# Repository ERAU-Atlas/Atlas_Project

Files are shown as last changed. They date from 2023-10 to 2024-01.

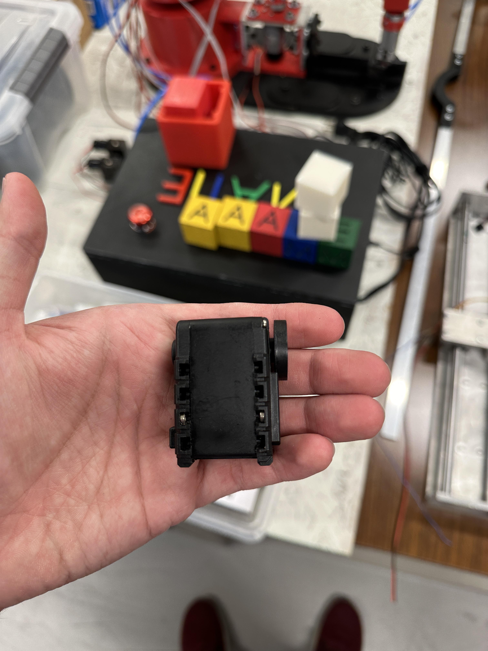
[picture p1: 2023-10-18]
Prelim/Milestones/Coceptual Design/Group CoDR/Group Conceptual Design Images/Servo pics/IMG_5382.jpeg

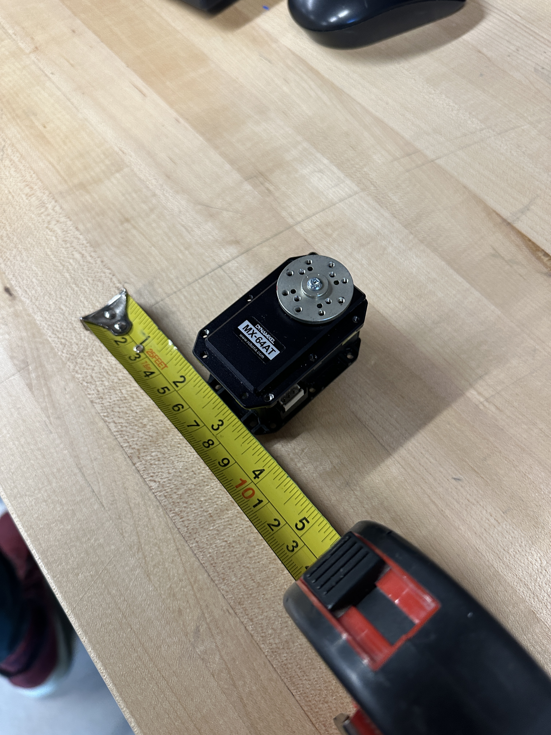
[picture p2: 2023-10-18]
Prelim/Milestones/Coceptual Design/Group CoDR/Group Conceptual Design Images/Servo pics/IMG_5388.jpeg

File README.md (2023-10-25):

# Atlas Project
The Atlas project is an ongoing robotics capstone design project at Embry-Riddle Aeronautical University. 
Our goal is to design and create a better way for furniture movement within residential buildings, to decrease the damages that accompany such moves.

## Documentation and other information can be found in the project [Wiki](https://github.com/ERAU-Atlas/Atlas_Project/wiki)

***

## Future Development notes and information will be noted below

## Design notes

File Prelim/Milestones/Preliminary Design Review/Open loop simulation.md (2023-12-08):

$$
F = \sum\limits_{i=1}^{N} F_{i}
$$

software flowchart instead of gantt chart

callouts instead of bullets

 resize top right pictures

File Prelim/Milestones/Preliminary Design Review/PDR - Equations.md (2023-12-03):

vector originating at B and terminating at C measured with respect to frame A

direction cosine matrix with columns that are the unit-basis vectors of frame B measured with respect to frame A

angular velocity of coordinate frame B relative to frame C measured with respect to frame A

matrix of moments of inertia and products of inertia of body B measured with respect to frame A

vector of first mass moments of body B measured in with respect to frame A

mass of body/particle i

translational momentum of body/particle i measured with respect to frame A

angular momentum of body/particle i about the origin of frame B measured with respect to frame A

force applied to body/particle i measured with respect to frame A

moment on body/particle i about point B measured with respect to frame A

vector of system forces along the system coordinates ${\boldsymbol a}$

***
Equations of motion:
$$
\boldsymbol{H}(\boldsymbol{\gamma})\ddot{\boldsymbol{\gamma}} + \boldsymbol{d}(\boldsymbol{\gamma}, \dot{\boldsymbol{\gamma}}) = \boldsymbol{F}_{\boldsymbol{\gamma}}
$$

***
position and orientation of Atlas:

$$
{^{I}_{I}{\boldsymbol{r}}_{F}} = \begin{bmatrix}\delta x \\ \delta y \\ \delta z\end{bmatrix}
$$
$$
{^{I}\boldsymbol{T}}_{\!F} = \left[\begin{array}{ccc} \cos\left(\psi \right)\,\cos\left(\theta \right) & -\cos\left(\theta \right)\,\sin\left(\psi \right) & \sin\left(\theta \right)\\ \cos\left(\phi \right)\,\sin\left(\psi \right)+\cos\left(\psi \right)\,\sin\left(\phi \right)\,\sin\left(\theta \right) & \cos\left(\phi \right)\,\cos\left(\psi \right)-\sin\left(\phi \right)\,\sin\left(\psi \right)\,\sin\left(\theta \right) & -\cos\left(\theta \right)\,\sin\left(\phi \right)\\ \sin\left(\phi \right)\,\sin\left(\psi \right)-\cos\left(\phi \right)\,\cos\left(\psi \right)\,\sin\left(\theta \right) & \cos\left(\psi \right)\,\sin\left(\phi \right)+\cos\left(\phi \right)\,\sin\left(\psi \right)\,\sin\left(\theta \right) & \cos\left(\phi \right)\,\cos\left(\theta \right) \end{array}\right]
$$
Where:
$\delta x$ = displacement in the x direction
$\delta y$ = displacement in the y direction
$\delta z$ = displacement in the z direction
$\phi$ = angle about the x axis
$\theta$ = angle about the y axis
$\psi$ = angle about the z axis

***

$$
\boldsymbol{{^{I}_{I}{\boldsymbol{r}}_{F}}} = \begin{bmatrix}\delta x \\ \delta y \\ \delta z\end{bmatrix}
$$

$$
{^{I}\boldsymbol{T}}_{\!F} = 
$$

$$
\left[\begin{array}{ccc} \cos\left(\psi \right)\,\cos\left(\theta \right) & -\cos\left(\theta \right)\,\sin\left(\psi \right) & \sin\left(\theta \right)\\ \cos\left(\phi \right)\,\sin\left(\psi \right)+\cos\left(\psi \right)\,\sin\left(\phi \right)\,\sin\left(\theta \right) & \cos\left(\phi \right)\,\cos\left(\psi \right)-\sin\left(\phi \right)\,\sin\left(\psi \right)\,\sin\left(\theta \right) & -\cos\left(\theta \right)\,\sin\left(\phi \right)\\ \sin\left(\phi \right)\,\sin\left(\psi \right)-\cos\left(\phi \right)\,\cos\left(\psi \right)\,\sin\left(\theta \right) & \cos\left(\psi \right)\,\sin\left(\phi \right)+\cos\left(\phi \right)\,\sin\left(\psi \right)\,\sin\left(\theta \right) & \cos\left(\phi \right)\,\cos\left(\theta \right) \end{array}\right]
$$

***

$$
{^{I}_{I}{\boldsymbol{r}}_{A3}} = {^{I}_{I}{\boldsymbol{r}}_{F}} + {^{I}\boldsymbol{T}}_{\!F} {^{F}_{F}{\boldsymbol{r}}_{A1}} + {^{I}\boldsymbol{T}}_{\!F} {^{F}\boldsymbol{T}}_{\!A1} {^{A1}_{A1}{\boldsymbol{r}}_{A2}} + {^{I}\boldsymbol{T}}_{\!F} {^{F}\boldsymbol{T}}_{\!A1} {^{A1}\boldsymbol{T}}_{\!A2} {^{A2}_{A2}{\boldsymbol{r}}_{A3}}
$$
$$
{^{I}\boldsymbol{T}}_{\!A3} = {^{I}\boldsymbol{T}}_{\!F} {^{F}\boldsymbol{T}}_{\!A1} {^{A1}\boldsymbol{T}}_{\!A2} {^{A2}\boldsymbol{T}}_{\!A3}
$$

where:
${^{I}_{I}{\boldsymbol{r}}_{1}}$
${_I^I}\mathbit{r}_1$

${^{A}_{B}{\boldsymbol{r}}_{}}$
${_B^A}r$

Planar two link IK:
$$
\theta_{2}= atan2\left(\pm \sqrt{1 - \left( \frac{z_{d}^{2} + y_{d}^{2} - l_{1}^{2} - l_{2}^{2}}{2l_{1}^{2}l_{2}^{2}}\right)^{2}}, \frac{z_{d}^{2} + y_{d}^{2} - l_{1}^{2} - l_{2}^{2}}{2l_{1}^{2}l_{2}^{2}} \right)
$$

$$
\begin{align*}
K_{1} &= l_{1} + l_{2} \cos(\theta_{2})\\
K_{2} &= l_{2}\sin(\theta_{2})
\end{align*}
$$

$$
\theta_{1} = atan2\left( z_{d}, y_{d} \right) - atan2\left( K_{2}, K_{1} \right)
$$

$$
{^{I}_{I}{\boldsymbol{r}}_{A3}} = {^{I}_{I}{\boldsymbol{r}}_{F}} + {^{F}_{F}{\boldsymbol{r}}_{A1}} + {^{A1}_{A1}{\boldsymbol{r}}_{A2}} + {^{A2}_{A2}{\boldsymbol{r}}_{A3}}
$$

$$
{^{I}_{I}{\boldsymbol{r}}_{A3}} = {^{I}_{I}{\boldsymbol{r}}_{F}} + {^{I}\boldsymbol{T}}_{\!F} {^{F}_{F}{\boldsymbol{r}}_{A1}} + {^{I}\boldsymbol{T}}_{\!F} {^{F}\boldsymbol{T}}_{\!A1} {^{A1}_{A1}{\boldsymbol{r}}_{A2}} + {^{I}\boldsymbol{T}}_{\!F} {^{F}\boldsymbol{T}}_{\!A1} {^{A1}\boldsymbol{T}}_{\!A2} {^{A2}_{A2}{\boldsymbol{r}}_{A3}}
$$

$$
{^{I}_{I}{\boldsymbol{r}}_{A3}} = {^{I}_{I}{\boldsymbol{r}}_{F}} + {^{I}\boldsymbol{T}}_{\!F} {^{F}_{F}{\boldsymbol{r}}_{A1}} + {^{I}\boldsymbol{T}}_{\!A1} {^{A1}_{A1}{\boldsymbol{r}}_{A2}} + {^{I}\boldsymbol{T}}_{\!A2} {^{A2}_{A2}{\boldsymbol{r}}_{A3}}
$$

***
Equations of motion

$$
\boldsymbol{H}(\gamma)\ddot{\gamma} + \boldsymbol{d}(\gamma, \dot{\gamma}) = \boldsymbol{F}_{\gamma}
$$

$$
\ddot{\boldsymbol{\gamma}} = \frac{\boldsymbol{F}_\gamma - \boldsymbol{d}(\gamma, \dot{\gamma})}{\boldsymbol{H}(\gamma)}
$$

$$
\ddot{\boldsymbol{\gamma}} = \frac{F_\gamma -\boldsymbol{d}(\gamma, \dot{\gamma}) + G - B\dot{\gamma} - Csign(\dot{\gamma})}{\boldsymbol{H}(\gamma)}
$$

***
### Runge-Kutta

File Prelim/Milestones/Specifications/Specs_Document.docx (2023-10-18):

SPECIFICATIONS DOCUMENT

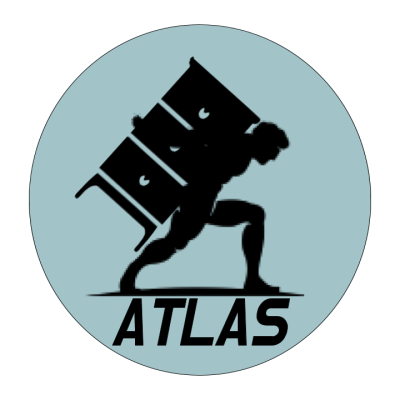
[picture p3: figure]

By

Ian Adelman

Devin Hoopes

Natalie Gonzalez

Alex Reinert

Submitted to Dr. Isenberg and Dr. Adams
of Embry-Riddle Aeronautical University
in Partial Fulfillment of the Course Requirements for ME 407 and COM 420

October 21, 2023

# ABSTRACT

In this document the proposed stair climbing system and its components will be described in detail, and an explanation for each component’s inclusion will be provided. Such explanation will be supplemented with the list of design requirements derived from the problem statement, and how each component/design feature directly contributes to fulfilling the requirements and solving the problem presented.

# 1.0 INTRODUCTION

In this section, the requirements will be laid out in the following categories: Functional, Sizing, and Safety.

## 1.1 PROBLEM STATEMENT

Transporting heavy furniture up and down the stairs is difficult and potentially dangerous.

To achieve the goal set by the problem statement, the requirements of function are as follows:

2.1.1 - The system shall transport furniture repeatedly up and down one floor within a residential building.

and Safety.

## 1.2 SYSTEM OVERVIEW

In this section the system will be shown, and the operation will be described in detail.

### 1.2.1 Components

### 1.2.2 Concept of Operations

The standard practice for operating the device is as follows: First, the user will load the payload furniture onto the platform and then apply securing straps through the side brackets. Next, use the remote control to command the device to begin walking up the set of stairs. Once the device reaches the top of the stairs, undo the straps and remove the furniture from the platform.

### 3.2.1 Process Flowchart

The following flowchart describes the process that the system will follow in order to achieve the problem statement.

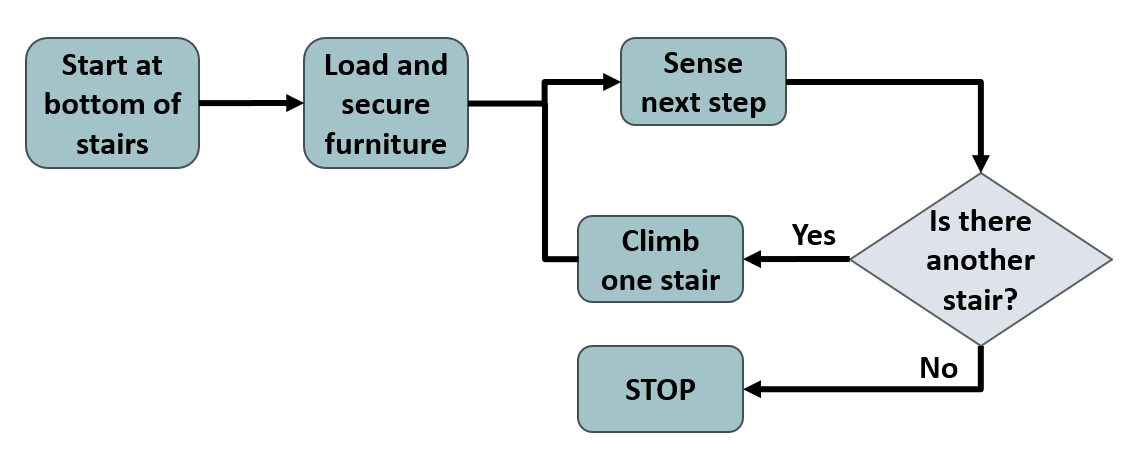
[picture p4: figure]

Figure 3.6: Process Flowchart

### 3.2.2 Hardware Block Diagram

The following block diagram describes the connections and relationships between the various components.

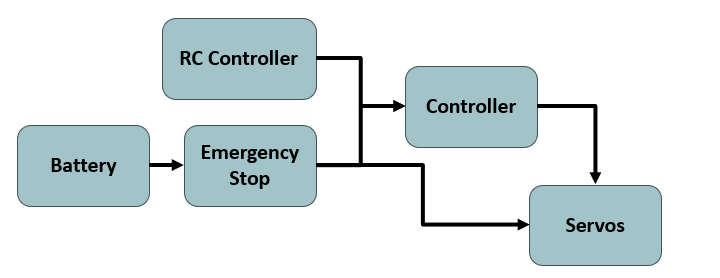
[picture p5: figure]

Figure 3.7: Hardware Block Diagram

# 2.0 REQUIREMENTS

In this section, the requirements will be laid out in the following categories: Functional, Sizing, and Safety.

## 2.1 FUNCTIONAL

To achieve the goal set by the problem statement, the requirements of function are as follows:

2.1.1 - The system shall transport furniture repeatedly up and down one floor within a residential building.

2.1.2 - The system shall accommodate up to a 4-seater sofa.

2.1.3 - The system shall accommodate up to a 5-shelf bookshelf.

2.1.4 - The system shall be reusable.

## 2.2 SIZING

To ensure that the system is of a proper size that is capable of being transported and capable of fitting within the stairwells it operates in, the requirements of interface are as follows:

2.2.1 - The system shall fit within a standard stairway according to Section R311.7.1 of the 2021 International Residential Code (IRC).

2.2.2 - The system shall be transportable in the back of an average American pickup truck in addition to the transported furniture.

## 2.3 SAFETY

To ensure that the system is overall safe, and does not endanger the operator or environment, the requirements of safety are as follows:

2.3.1 - The system shall cause less injury and strain than an average moving job.

2.3.2 - The system shall not destructively alter the environment.

2.3.3 - The system shall not damage the furniture.

# 3.0 SYSTEM OVERVIEW

In this section the system will be shown, and the operation will be described in detail.

## 3.1 SYSTEM COMPONENTS

In this section the system’s components will be described in detail, with an explanation of how each requirement is met through the design’s features.

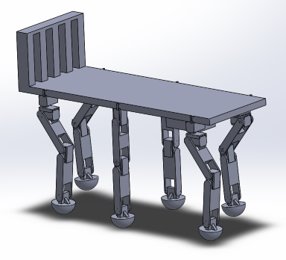
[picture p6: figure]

Electronics

Platform

2 DOF Legs

Brackets

3 DOF Legs

Figure 3.1: Complete Drawing

### 3.1.1 Platform

In the figure below, the dimensions of the platform are shown.

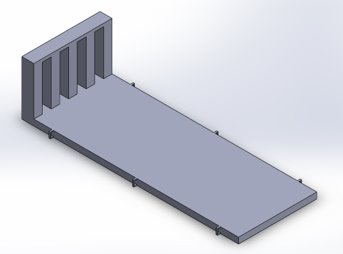
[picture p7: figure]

8”

13”

36”

Figure 3.2: Platform Drawing

To accommodate its payload [2.1.2, 2.1.3] as well as fit into a standard residential stairwell [2.2.1] or pickup truck bed [2.2.2], the system is sized to be 25” at full scale, allowing for an inch of space between the system and the stairs’ thinnest point, the rails.

### 3.1.2 Brackets

In the figure below, the dimensions of the bracket are shown.

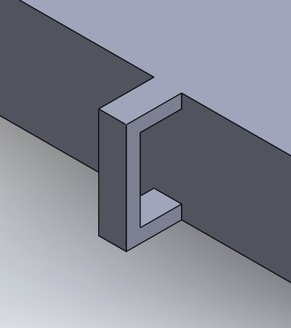
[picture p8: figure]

0.125”

0.25”

1”

Figure 3.3: Bracket Drawing

To prevent the payload from slipping, thus damaging the furniture as well as the surrounding environment [2.3.2, 2.3.3], brackets are located along the edge of the platform to allow for straps to be applied to the payload.

### 3.1.3 Legs

In the figure below, the dimensions of the robotic leg are shown.

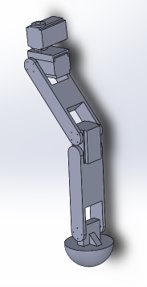
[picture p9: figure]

7.2””

7.2””

Figure 3.4: Robotic Leg Drawing

In order to ascend the stairs [2.1.1] without modifying the surrounding environment [2.3.2], the system will utilize a set of legs for locomotion. The front and back pairs of legs each have 3 degrees of freedom, with a 2 degree of freedom shoulder as well as a 1 degree of freedom elbow provide the majority of the force required to ascend the stairs. Providing stability [2.3.2, 2.3.3] rather than climbing force, the pair of central legs have 2 degrees of freedom each, with a 1 degree of freedom shoulder and elbow. Additionally, to prevent damage to the stairwell flooring [2.3.2] each leg has a semicircular rubber foot.

### 3.1.4 Electronics

In the figure below, the dimensions of the electronics bay are shown.

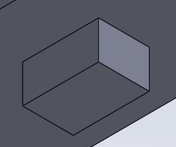
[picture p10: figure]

3”

4”

6”

Figure 3.5: Electronics Bay Drawing

In order for the system to be reusable [2.1.4], the system will have a rechargeable battery. In order to reduce the strain and injury to a person [2.3.1], the system will be remotely controlled. In order to ascend the stairs [2.1.1], the system will have an encoder to detect the depth of each step and the height of the next step.

## 3.2 CONCEPT OF OPERATIONS

The standard practice for operating the device is as follows: First, the user will load the payload furniture onto the platform and then apply securing straps through the side brackets. Next, use the remote control to command the device to begin walking up the set of stairs. Once the device reaches the top of the stairs, undo the straps and remove the furniture from the platform.

### 3.2.1 Process Flowchart

The following flowchart describes the process that the system will follow in order to achieve the problem statement.

Figure 3.6: Process Flowchart

### 3.2.2 Hardware Block Diagram

The following block diagram describes the connections and relationships between the various components.

Figure 3.7: Hardware Block Diagram

# 4.0 CONCLUSION

Through the above features, the system can reliably and safely transport its intended loads up and down a flight of stairs without endangering the operator and while reducing the overall strain on the operator compared to manually moving the payload up the stairs.

# 5.0 APPENDIX

Below is the appendix, including the requirements verification matrix and the decision matrix created for the project.

## 5.1 APPENDIX A – REQUIREMENTS VERIFICATION MATRIX

No. | Requirement | Verification Description | T | A | O | R
1 | 2.1.1 | Test load and trial | X
2 | 2.1.2 | Measurement/Trial | X
3 | 2.1.3 | Measurement/Trial | X
4 | 2.1.4 | Repeated Trials | X | | X
5 | 2.2.1 | Measurement and Comparison | X | | | X
6 | 2.2.2 | Measurement and Comparison | X | | | X
7 | 2.3.1 | Trial, followed by Analysis and Comparison | X | X | X | X
8 | 2.3.2 | Trial and Observation | X | | X
9 | 2.3.3 | Trial and Observation | X | | X

T – Test and Measurement; A – Analysis and Simulation;
O – Observation and Inspection; R – Reference and Datasheet

(Requirements verification matrix. | download table - researchgate) [1]

## 5.2 APPENDIX B – DECISION MATRIX

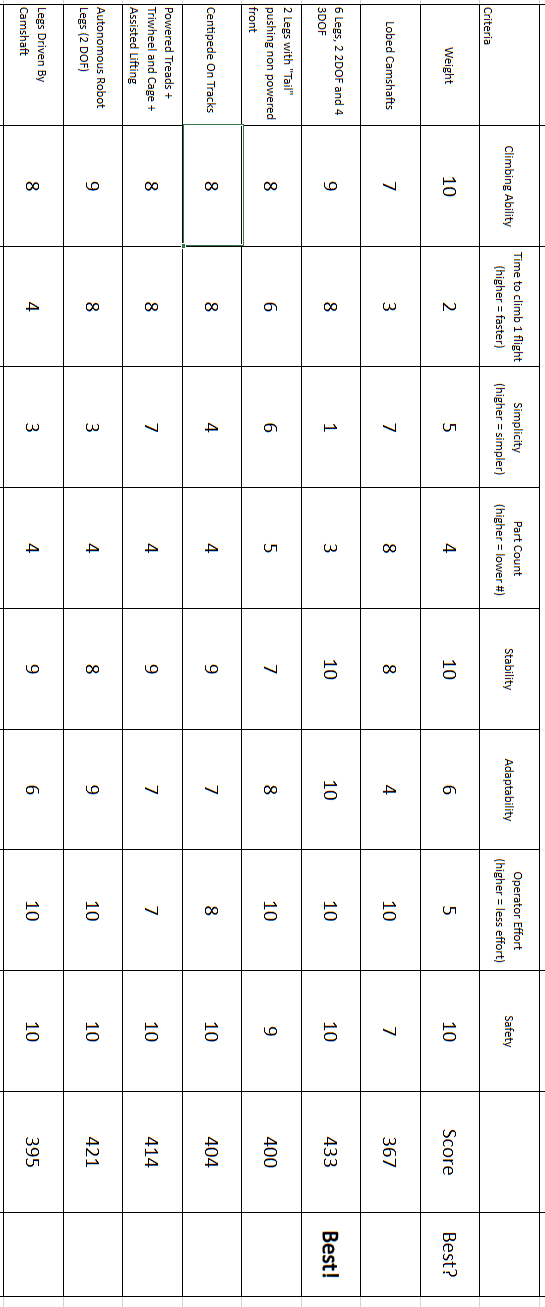
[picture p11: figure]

## 5.3 APPENDIX C – MORPHOLOGICAL CHART

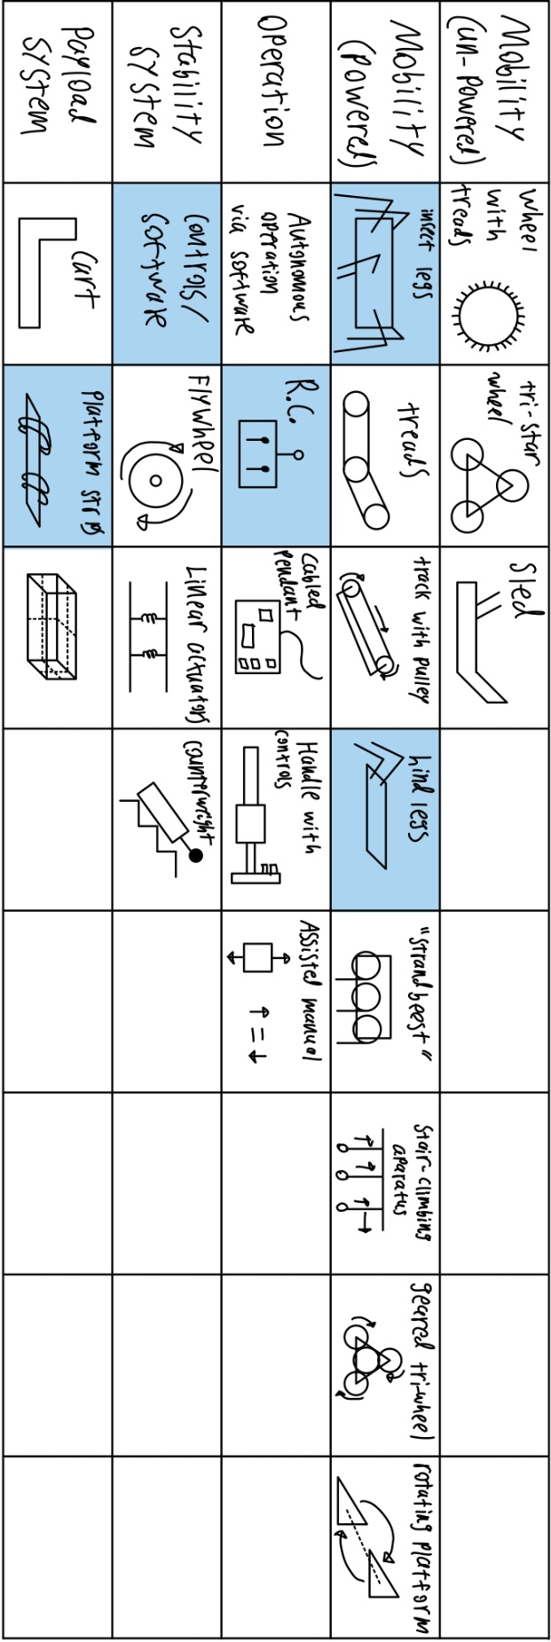
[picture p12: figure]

# 6.0 REFERENCES

[1]
“Requirements verification matrix. | download table - researchgate,” ResearchGate, https://www.researchgate.net/figure/Requirements-Verification-Matrix_tbl1_269163835 (accessed Sep. 28, 2023).

Specs for codes:

https://codes.iccsafe.org/content/IRC2021P2/chapter-3-building-planning

R311.7.1 Width.

Stairways shall be not less than 36 inches (914 mm) in clear width at all points above the permitted’

The maximum width of the system shall not exceed 27 inches at full scale, reducing to a maximum width of 13 inches at the designed scale.

Pull from page, use scale?

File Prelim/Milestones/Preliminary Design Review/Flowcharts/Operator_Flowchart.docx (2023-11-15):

Operator

END

START

Remove straps and PAYLOAD.

Turn OFF system with communications device.

Roll away from stairway.

NO

YES

YES

Done Climbing?

E

Select BOTTOM-STEP CLIMBING mode.

YES

YES

NO

At Bottom Step?

UP or DOWN?

E

E

E

Select DESCENDING mode.

Select FLAT mode.

NO

Done Climbing?

At Landing?

E

NO

NO

At stairway yet?

YES

Select TOP-STEP CLIMBING mode.

Select ASCENDING mode.

UP

E

At Landing?

Select FLAT mode.

Turn ON system with communications device.

Place PAYLOAD on platform and secure with straps.

END

EMERGENCY SHUTOFF

END

Press EMERGENCY BUTTON.

Anything dangerous with operation?

E

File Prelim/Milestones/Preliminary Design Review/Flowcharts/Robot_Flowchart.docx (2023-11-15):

Robot

E

Turn OFF.

Roll away from stairway.

NO

YES

YES

YES

Switch to FLAT mode.

NO

Done Climbing?

NO

At Bottom Step?

Switch to BOTTOM-STEP CLIMBING mode.

Done Climbing?

YES

NO

Switch to TOP-STEP CLIMBING mode.

UP or DOWN?

At Landing?

DOWN

Switch to DESCENDING mode.

UP

Switch to ASCENDING mode.

Drive to stairway.

Switch to FLAT mode.

Turn ON.

START

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
EMERGENCY SHUTOFF

END

SHUT OFF ALL POWER.

YES

NO

EMERGENCY Button Pressed?

E

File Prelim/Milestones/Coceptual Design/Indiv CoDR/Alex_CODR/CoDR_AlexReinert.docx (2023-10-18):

CONCEPTUAL DESIGN DOCUMENT


By

Alex Reinert

Submitted to Dr. Isenberg and Dr. Adams
of Embry-Riddle Aeronautical University
in Partial Fulfillment of the Course Requirements for ME 407 and COM 420

9/29/23

# ABSTRACT

The following document introduces the design that is a solution to the problem statement below. The design’s components and features will be discussed and detailed explanation of how they solve the requirements to the problem.

# 1.0 PROBLEM STATEMENT

Transporting heavy furniture up and down the stairs is difficult and potentially dangerous.

# 2.0 REQUIREMENTS

## 2.1 FUNCTION

To achieve the goal set by the problem statement, the requirements of function are as follows:

2.1.1 - The system shall transport furniture repeatedly up and down one floor within a residential building.

2.1.2 - The system shall accommodate up to a 4-seater sofa.

2.1.3 - The system shall accommodate up to a 5-shelf bookshelf.

2.1.4 - The system shall be reusable.

## 2.2 INTERFACING

To ensure that the system is of a proper size that is capable of being transported and capable of fitting within the stairwells it operates in, the requirements of interface are as follows:

2.2.1 - The system shall fit within a standard stairway according to Section R311.7.1 of the 2021 International Residential Code (IRC)

2.2.2 - The system shall be transportable in the back of an average American pickup truck in addition to the transported furniture.

## 2.3 SAFETY

To ensure that the system is overall safe, and does not endanger the operator or environment, the requirements of safety are as follows:

2.3.1 - The system shall cause less injury and strain than an average moving job.

2.3.2 - The system shall not destructively alter the environment.

2.3.3 - The system shall not damage the furniture.

# 3.0 SYSTEM OVERVIEW

## 3.1 CONCEPT OF OPERATIONS

The standard practice for using the proposed device is as follows: First, the user will load the furniture onto the flat platform and put on securing straps to ensure the furniture is stable. Second, the user will place it in front on the stairs. Third, the user will turn on the hardware and motors will begin to run. Fourth, the ultrasonic sensor will detect a stairway and begin increasing speed to the motors. Fifth, the tilt sensor will sense that we are approaching a landing and will slow down the motors. Sixth, the system will stop after reaching the landing. Finally, the straps will be removed, and furniture will be picked up and placed where it is needed.

## 3.2 SYSTEM DESIGN

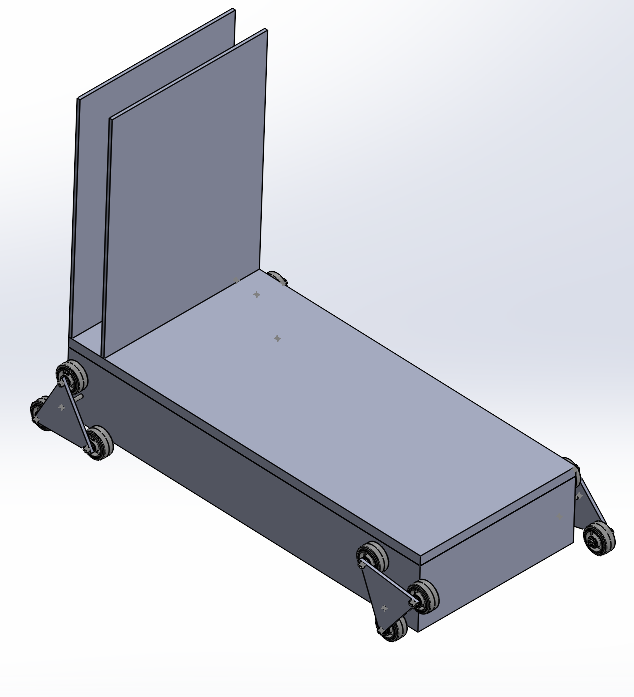
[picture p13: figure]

Tri-Star Wheel

Electronic Storage

Composite Bed

Spring-Backing

### 3.2.1 Composite Bed

The system includes a flat platform where the furniture is set and secured before operation. The furniture rests on the flat platform and is kept secure with straps ensuring both the safety of the furniture itself and the environment around it, satisfying requirements 2.3.2 and 2.3.3. The platform is sized so that its width does not exceed 26.5 inches and 60 inches long. This is big enough to support a 4-seater sofa and a 5-shelf bookshelf, satisfying requirements 2.1.2 and 2.1.3. This will also fit into the back of a pickup truck and meet the standard of the minimum width of a stairwell according to the IRC residential code, this satisfies requirements 2.2.1 and 2.2.2.

### 3.2.2 Tri-Star Wheel

The system is driven by four DC motors attached to four triangles. The motor drives an axle located at the center of each triangle. The system also includes three wheels attached by an axle to each point on the triangle. Both feature’s help meet requirement 2.1.1.

### 3.2.3 Spring-Backing

The system is fitted with four compression springs in between two rectangular plates, which provides support to the system. This Spring-Backing can compress to support heavy weight moving up or down the stairs, satisfying requirement 2.1.4.

### 3.2.4 Electronics

The system is fitted with a rechargeable battery located in the Electronic Storage, which provides the necessary power to the rest of the system satisfying requirement 2.1.4. The system also includes two sensors, an ultrasonic sensor and a tilt sensor, this will ultimately control the motor speed, satisfying requirements 2.3.1 and 2.3.3. The system also includes four DC motors that turn the Tri-Star Wheel, satisfying requirement 3.3.1.

### 3.2.5 Software

The software design is to take input from the ultrasonic sensor to see how far away the staircase is and a tilt sensor to detect when we are on a landing or on the stairs. It then takes this information to compute the appropriate motor speed in order to elevate up the stairs.

## 3.3 OTHER SOLUTIONS

### 3.3.1 Stair Climber for Caskets

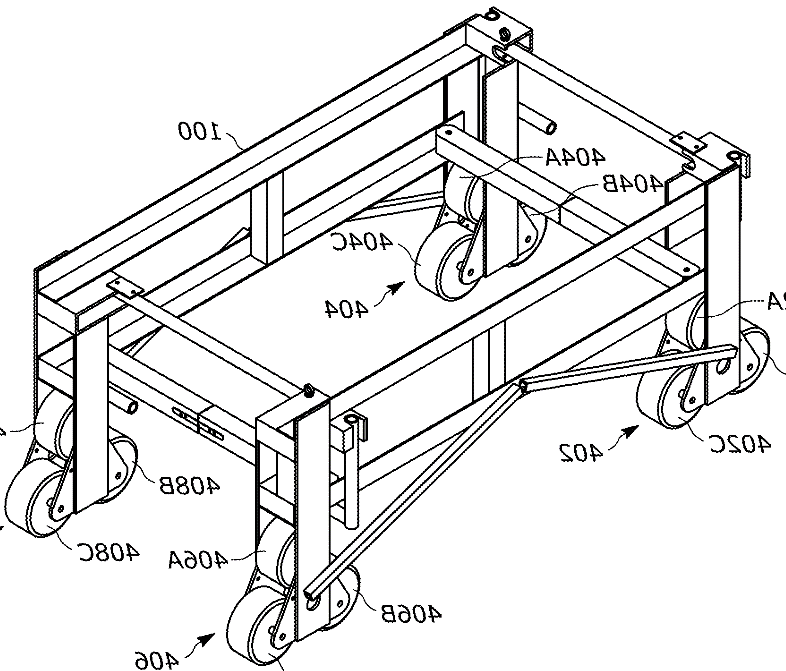
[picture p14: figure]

Tri-Star Wheel

The image above is the Stair Climber for Caskets invented by Samuel Polumbo. This design is not powered and intended for a user to grab the handles and pull the device up the stairs. It moves up the stairs with the Tri-Star Wheel pivoting up each step.

# 4.0 CONCLUSION

From the above features and components, the system can safely and securely move furniture up or down the stairs. It can accommodate the intended furniture that is to be placed on it and not endanger the user of the system.

# 5.0 APPENDIX

No. | Requirement | Verification Description | T | A | O | R
1 | 2.1.1 | Test load and trial | X
2 | 2.1.2 | Measurement/Trial | X
3 | 2.1.3 | Measurement/Trial | X
4 | 2.1.4 | Repeated Trials | X | | X
5 | 2.2.1 | Measurement and Comparison | X | | | X
6 | 2.2.2 | Measurement and Comparison | X | | | X
7 | 2.3.1 | Trial, followed by Analysis and Comparison | X | X | X | X
8 | 2.3.2 | Trial and Observation | X | | X
9 | 2.3.3 | Trial and Observation | X | | X

T – Test and Measurement; A – Analysis and Simulation;
O – Observation and Inspection; R – Reference and Datasheet

(Requirements verification matrix. | download table - researchgate) [1]

# 6.0 ACKNOWLEDGEMENTS

This design directly implemented the Tri-Star Wheel from the casket stair climber, which was invented by Samuel Palumbo, found in US patent US11691660B2 [2].

# 7.0 REFERENCES

[1]
“Requirements verification matrix. | download table - researchgate,” ResearchGate, https://www.researchgate.net/figure/Requirements-Verification-Matrix_tbl1_269163835 (accessed Sep. 28, 2023).

[2]

Palumbo JR., Samuel, “Stair Climber for Casket,” US11691660B2, Jul. 04, 2023 Accessed: Sep. 14, 2023. [Online]. Available: https://patents.google.com/patent/US11691660B2/en?q=(stair+climber)&oq=stair+climber

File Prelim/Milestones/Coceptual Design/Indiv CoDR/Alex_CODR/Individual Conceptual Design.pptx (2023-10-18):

## Individual Conceptual Design

- By:
- Alex Reinert

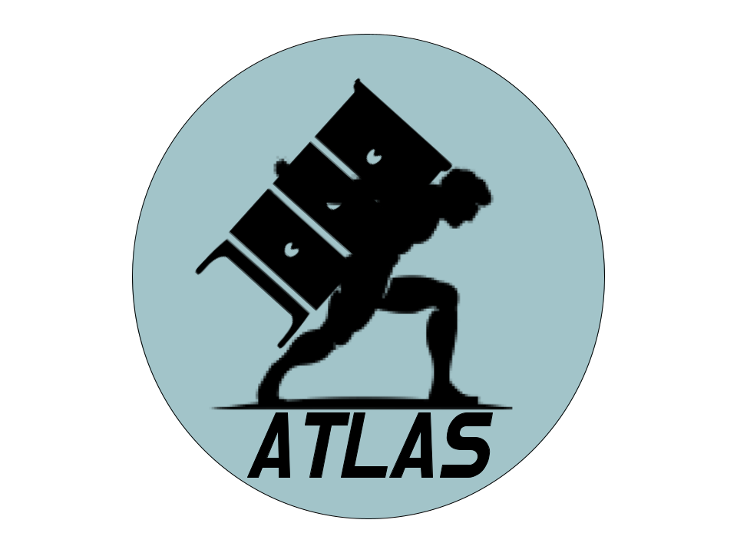
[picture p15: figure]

## Agenda

Design Requirements

Design

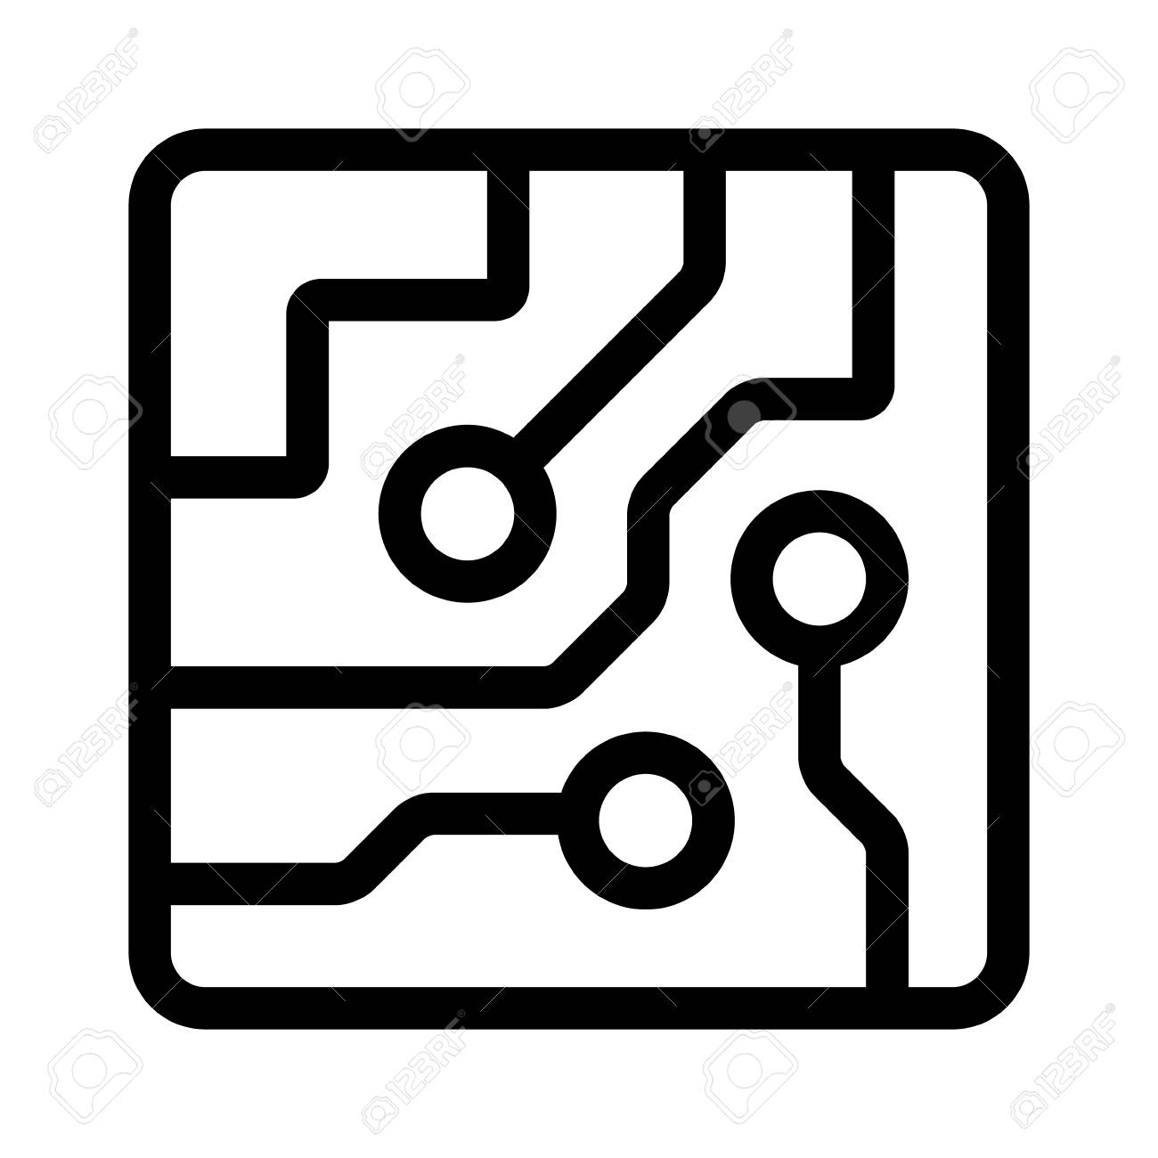
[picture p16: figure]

Electrical Components

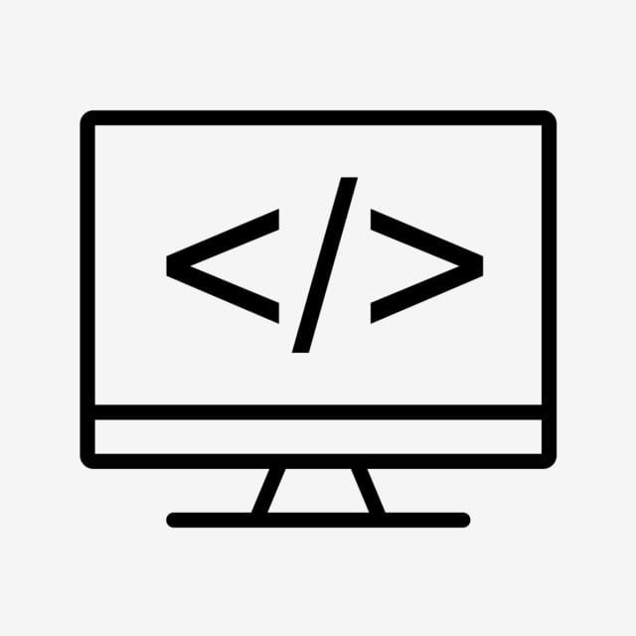
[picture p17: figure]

Coding

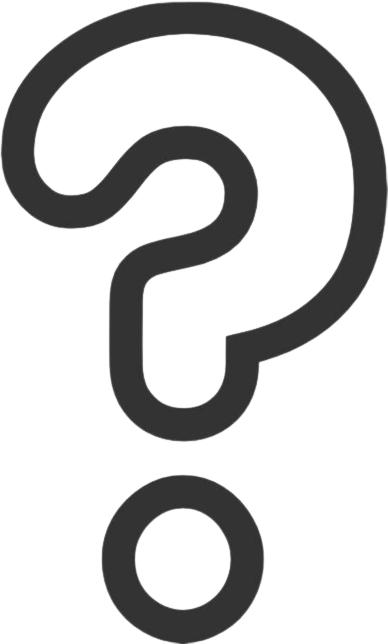
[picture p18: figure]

Introduction

Questions

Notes: Ian Slide

## Introduction

</>

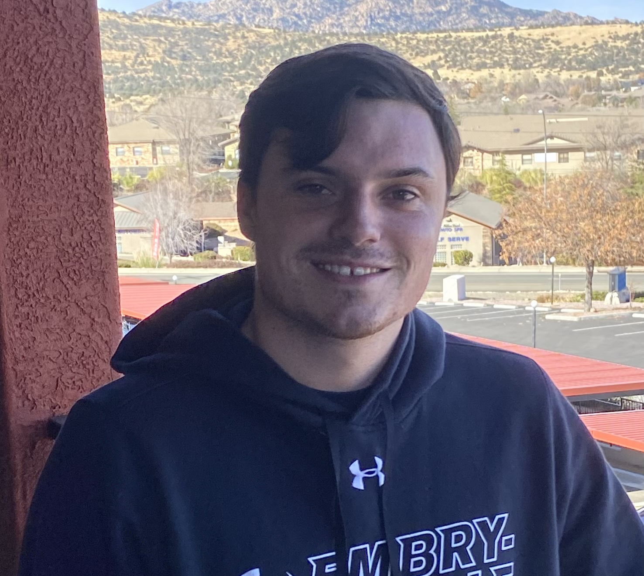
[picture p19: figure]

- Alex Reinert
- Systems Engineer

## Review of the Problem Statement

</>

Transporting heavy furniture up or down one flight of straight stairs is difficult and potentially dangerous.

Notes: Natalie Slide

## Review of Design Requirements

</>

1.1 The system shall cause less injury and strain than an average moving job.
1.2 The system shall not destructively alter the environment.
1.3 The system shall not damage the furniture.
2.1 The system shall transport furniture repeatedly up or down one floor within a residential building.
2.2 The system shall accommodate up to a 4-seater sofa.
2.3 The system shall accommodate up to a 5-shelf bookshelf.
2.4 The system shall be reusable.
3.1 The system shall fit within a standard stairway according to Section R311.7.1 of the 2021 International Residential Code (IRC).
3.2 The system shall be transportable in the back of an average American pickup truck in addition to the transported furniture.

## Design

</>


Spring-Backing

Composite bed

Tri-star Wheel

Electronic Storage

## Design

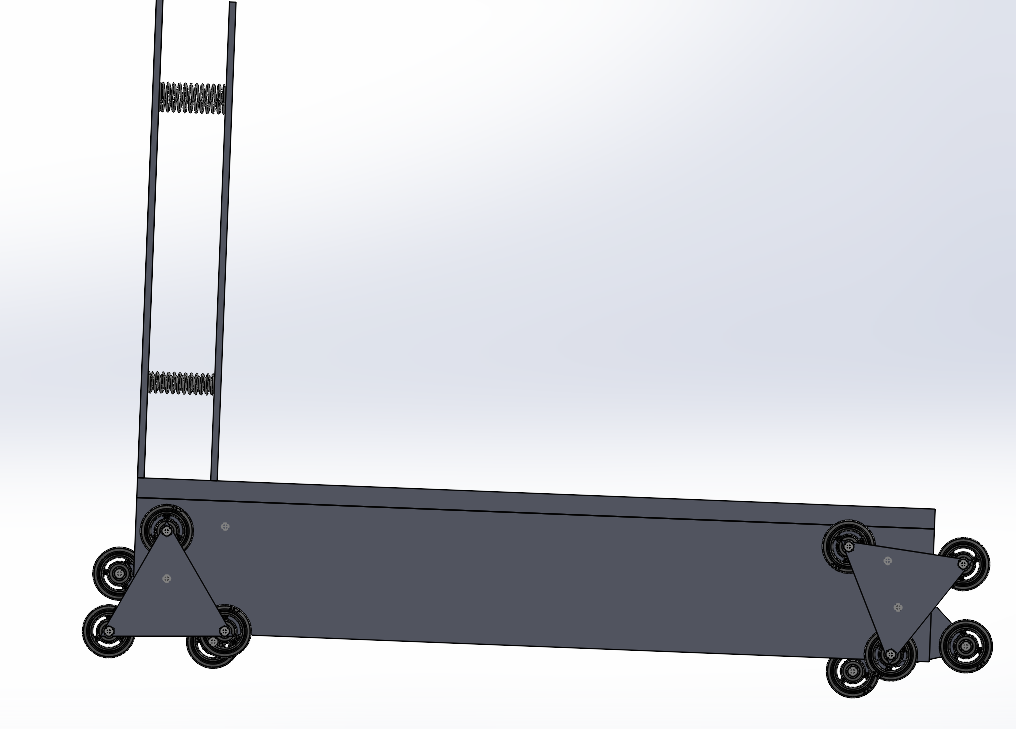
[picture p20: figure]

Springs

## Electrical Components

</>

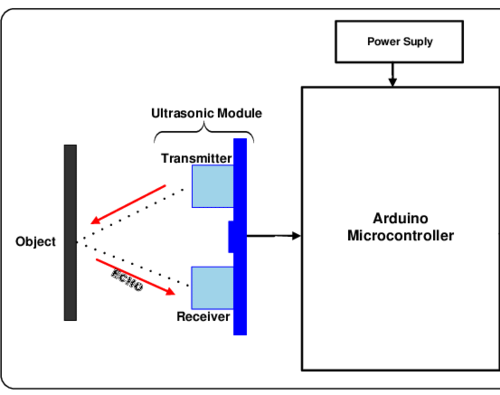
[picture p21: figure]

Ultrasonic Sensor

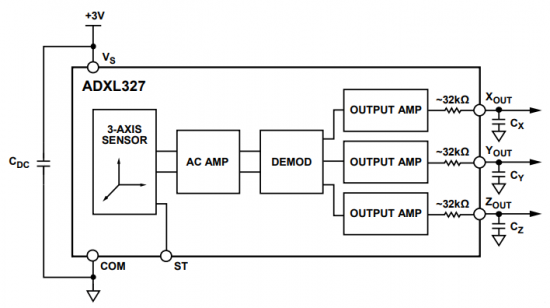
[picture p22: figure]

Tilt Sensor

## Electrical Components

</>

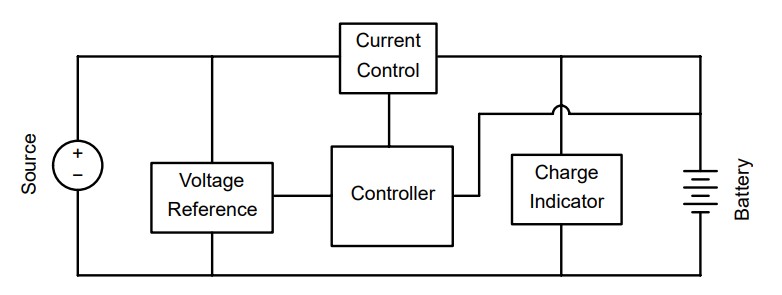
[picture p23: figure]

Rechargeable Battery

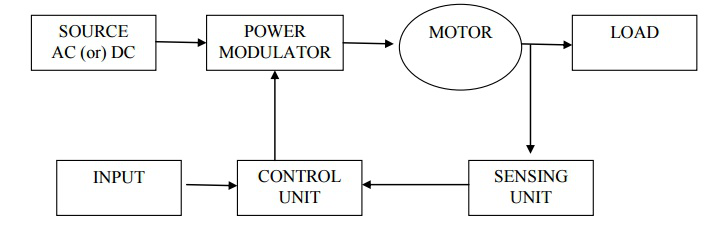
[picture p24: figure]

Generic Motor Block Diagram

## Coding

</>

Start

Turn on motor

Does Ultrasonic Sensor detect an object?

Keep constant motor speed

True

Increase speed to motors to go upstairs

Does tilt sensor detect an incline?

False

Decrease Speed for going downstairs

Does tilt sensor detect a landing?

False

Does tilt sensor detect a landing?

Does tilt sensor detect a landing?

True

True

False

Keep constant motor speed

Slow down motor for flat surface

False

True

Increase speed for flat surface

Keep constant motor speed

Stop

## Questions?

</>

## References

- Getz, R. (2021). Functional Block Diagram of ADXL327. Analog Devices. Retrieved September 24, 2023, from https://wiki.analog.com/university/labs/2_axis_tilt_sensor_adalm2000.
- Kart, B. (2018). Block Diagram of an Electrical Drives. Brain Kart. Retrieved September 24, 2023, from https://www.brainkart.com/article/Block-Diagram-of-an-Electrical-Drives_12673/.
- McMaster-Carr, T. (2017a). Compression Spring. United States; McMaster-Carr.
- McMaster-Carr, T. (2017b). High-Strength Rubber Wheel. China; McMaster-Carr.
- McMaster-Carr, T. (2017c). Rotary Shaft. United States; McMaster-Carr.
- McMaster-Carr, T. (2017d). Zinc-Plated Steel Wheel Axle. China; McMaster-Carr.
- Orji, E. (2018). System Block Diagram. ResearchGate. Retrieved September 24, 2023, from https://www.researchgate.net/figure/System-Block-Diagram_fig1_336253681.
- Sheppard, J. (2021). Basics of Battery Charging Circuit Design. Battery Power Tips. Retrieved September 24, 2023, from https://www.batterypowertips.com/basics-of-battery-charging-circuit-design-faq/.

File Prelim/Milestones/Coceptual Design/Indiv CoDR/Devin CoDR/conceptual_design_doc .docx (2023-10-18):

CONCEPTUAL DESIGN DOCUMENT


By

Devin Hoopes

Submitted to Dr. Isenberg and Dr. Adams
of Embry-Riddle Aeronautical University
in Partial Fulfillment of the Course Requirements for ME 407 and COM 420

9/28/23

# ABSTRACT

In this document the proposed system and its components will be described in detail, and an explanation for each component’s inclusion will be provided. Such explanation will be supplemented with the list of design requirements derived from the problem statement, and how each component/design feature directly contributes to fulfilling the requirements and solving the problem presented.

# 1.0 PROBLEM STATEMENT

Transporting heavy furniture up and down the stairs is difficult and potentially dangerous.

# 2.0 REQUIREMENTS

## 2.1 FUNCTION

To achieve the goal set by the problem statement, the requirements of function are as follows:

2.1.1 - The system shall transport furniture repeatedly up and down one floor within a residential building.

2.1.2 - The system shall accommodate up to a 4-seater sofa.

2.1.3 - The system shall accommodate up to a 5-shelf bookshelf.

2.1.4 - The system shall be reusable.

## 2.2 INTERFACING

To ensure that the system is of a proper size that is capable of being transported and capable of fitting within the stairwells it operates in, the requirements of interface are as follows:

2.2.1 - The system shall fit within a standard stairway according to Section R311.7.1 of the 2021 International Residential Code (IRC)

2.2.2 - The system shall be transportable in the back of an average American pickup truck in addition to the transported furniture.

## 2.3 SAFETY

To ensure that the system is overall safe, and does not endanger the operator or environment, the requirements of safety are as follows:

2.3.1 - The system shall cause less injury and strain than an average moving job.

2.3.2 - The system shall not destructively alter the environment.

2.3.3 - The system shall not damage the furniture.

# 3.0 SYSTEM OVERVIEW

## 3.1 CONCEPT OF OPERATIONS

The standard practice for using the proposed device is as follows: First, the user will load the furniture onto the cart section and apply securing straps to ensure the stability of the system. Second, the user will grab hold of the handle at the front of the device and pull to guide the system up the staircase, taking care to avoid obstacles. Third, once the device has reached the upper landing the handle will be released, and the furniture removed from its straps.

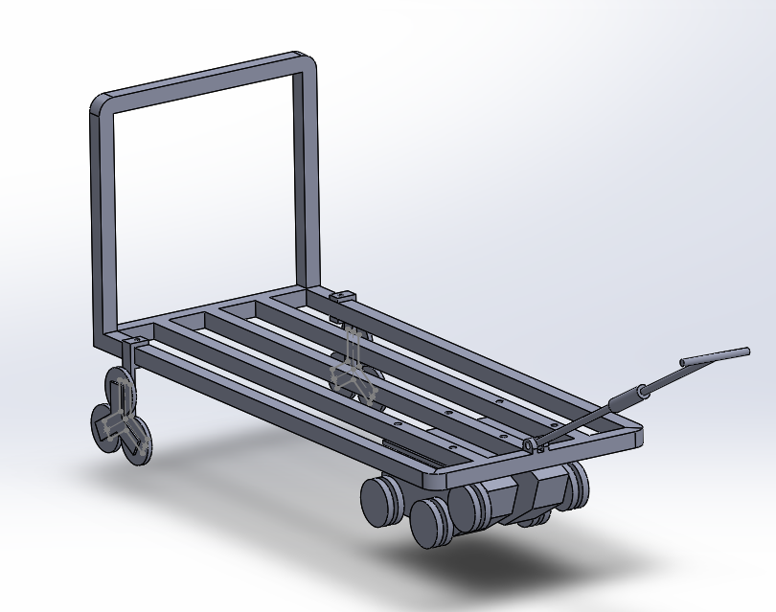
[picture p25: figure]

## 3.2 SYSTEM COMPONENTS

Tread Block

Back Wheels

Cart

Handle

### 3.2.1 Platform

60”

25”

The system includes a cart-like platform where the payload is set and secured before operation. The furniture rests on the cart and is kept secure with straps ensuring both the safety of the furniture itself and the environment around it, fulfilling requirements 2.3.2 and 2.3.3. The platform is sized so that its width does not exceed 25 inches, which fits both into the back of a pickup truck and within the minimum width of a stairwell according to the IRC residential code, thus fulfilling requirements 2.2.1 and 2.2.2.

### 3.2.2 Propulsion

The system is driven by a central motor and given additional torque by means of a gearbox. The motor drives a pair of treads located at the front of the system, while an unpowered pair of back wheel arrays. The front end of the tread block is angled upwards to better catch the edge of a stair and pull itself up, while the back wheels are arranged in order to roll up the stairs smoother than a single wheel would allow. Both features are required to fulfil requirements 2.1.1, 2.1.2, and 2.1.3 by providing the force necessary to lift the loaded system upwards, and by providing the necessary grip and support on an uneven surface respectively. Additionally, by providing the majority of the work involved in moving the furniture the amount of work required by the operator is severely reduced, thus greatly reducing the risk of injury and satisfying requirement 2.3.1.

### 3.2.3 Electronics

The system is fitted with a battery located in the tread block, which provides the necessary power to the rest of the system. This battery can be recharged, thus fulfilling requirement 2.1.4. The system also includes a control handle that works to keep the system a safe distance from the user while also requiring a minimal amount of force to activate. Combined with a dead man’s switch located on the handle, the system requires human oversight to act and is thus unlikely to ram into obstacles or the operator, fulfilling requirements 2.3.1 and 2.3.3

# 4.0 CONCLUSION

Through the above features, the system can reliably and safely transport its intended loads up and down a flight of stairs without endangering the operator and while reducing the overall strain on the operator compared to manually moving the payload up the stairs.

# 5.0 APPENDIX

No. | Requirement | Verification Description | T | A | O | R
1 | 2.1.1 | Test load and trial | X
2 | 2.1.2 | Measurement/Trial | X
3 | 2.1.3 | Measurement/Trial | X
4 | 2.1.4 | Repeated Trials | X | | X
5 | 2.2.1 | Measurement and Comparison | X | | | X
6 | 2.2.2 | Measurement and Comparison | X | | | X
7 | 2.3.1 | Trial, followed by Analysis and Comparison | X | X | X | X
8 | 2.3.2 | Trial and Observation | X | | X
9 | 2.3.3 | Trial and Observation | X | | X

T – Test and Measurement; A – Analysis and Simulation;
O – Observation and Inspection; R – Reference and Datasheet

(Requirements verification matrix. | download table - researchgate) [1]

# 6.0 ACKNOWLEDGEMENTS

The design of the back wheel array is greatly inspired by the invention of Samuel Palumbo, found in US patent US11691660B2 [2] and significantly contributed to the design.

# 7.0 REFERENCES

[1]
“Requirements verification matrix. | download table - researchgate,” ResearchGate, https://www.researchgate.net/figure/Requirements-Verification-Matrix_tbl1_269163835 (accessed Sep. 28, 2023).

[2]

Palumbo JR., Samuel, “Stair Climber for Casket,” US11691660B2, Jul. 04, 2023 Accessed: Sep. 14, 2023. [Online]. Available: https://patents.google.com/patent/US11691660B2/en?q=(stair+climber)&oq=stair+climber

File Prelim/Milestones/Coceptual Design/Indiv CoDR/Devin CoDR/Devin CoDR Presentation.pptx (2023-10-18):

## Robotic Legs Conceptual Design

- By:
- Ian Adelman


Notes: Ian slide

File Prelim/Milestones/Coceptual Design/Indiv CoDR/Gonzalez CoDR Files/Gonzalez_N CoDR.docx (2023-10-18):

CONCEPTUAL DESIGN DOCUMENT


By

Natalie Gonzalez

Submitted to Dr. Isenberg and Dr. Adams
of Embry-Riddle Aeronautical University
in Partial Fulfillment of the Course Requirements for ME 407 and COM 420

9/29/23

# ABSTRACT

This conceptual design review presents an innovative stairlift system aimed at revolutionizing mobility solutions for individuals with and without limited mobility or disabilities. Traditional staircases have long presented challenges for all, necessitating the need for assistive devices. The proposed stair lift system offers a novel approach to address these challenges by providing a safe, efficient, and user-friendly solution for navigating stairs.

# 1.0 PROBLEM STATEMENT

Transporting heavy furniture up or down one flight of stairs is difficult and potentially dangerous.

# 2.0 REQUIREMENTS

## 2.1 FUNCTION

To achieve the goal set by the problem statement, the requirements of function are as follows:

2.1.1 - The system shall transport furniture repeatedly up or down one floor within a residential building.

2.1.2 - The system shall accommodate up to a 4-seater sofa.

2.1.3 - The system shall accommodate up to a 5-shelf bookshelf.

2.1.4 - The system shall be reusable.

## 2.2 INTERFACING

To ensure that the system is of a proper size that is capable of being transported and capable of fitting within the stairwells it operates in, the requirements of interface are as follows:

2.2.1 - The system shall fit within a standard stairway according to Section R311.7.1 of the 2021 International Residential Code (IRC)

2.2.2 - The system shall be transportable in the back of an average American pickup truck in addition to the transported furniture.

## 2.3 SAFETY

To ensure that the system is overall safe, and does not endanger the operator or environment, the requirements of safety are as follows:

2.3.1 - The system shall cause less injury and strain than an average moving job.

2.3.2 - The system shall not destructively alter the environment.

2.3.3 - The system shall not damage the furniture.

# 3.0 SYSTEM OVERVIEW

## 3.1 Previous Design

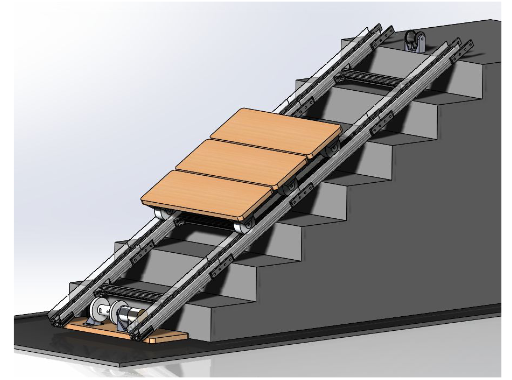
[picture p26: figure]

Figure 1: Previous Design [1]

This is a previous design that inspired the design of the system below. In this design a winch and pulley system are used to pull items upstairs, in order to bypass going up each step a rail system was created. The system also moves much like a conveyer belt. Issues I found with this design were that it is not practical for heavy furniture since the system has a flat base for the items to be placed on, even items with low weight could easily slide off. This could cause damage to the user and/or the item, failing to meet our requirements [2.3.1,2.3.3]. Another issue we found with this design is that it must be mounted to the stairs, which would not satisfy our requirements [2.3.2]. The last issue I found is that the rails must be set at a certain distance apart and that may not be within the minimum standards of stair widths which is mentioned above in the requirements [2.2.1].


Figure 2: Free Body Diagram of Existing Design [1]

## 3.2 CONCEPT OF OPERATIONS

The basic procedure to using this machine is to load a large piece of furniture onto the apparatus then set the system to transport the furniture up the stairs. This system should allow the user to select a direction then drive in that direction. The drive system for this design is a winch connected to a sled and a pulley creating a closed system to control the motion of the sled. The main safety feature of this system is a sensor that reads what is in front and behind the system, that is its stopping mechanism.

### 3.2.1 System Flowchart


Figure 3: Flowchart of System

Above is a high-level example of how the system will work with its inputs. Once the system is turned on the user must input the direction they would like to go, then the system will continually receive readings from the sensors. If and when the sensors read a distance value that is too small to be acceptable the system will implement a stop.

### 3.2.2 System Overview


Figure 4: Entire System Assembly

The entire system can cover up to 20 feet which is well within the standards specified in the requirements [2.2.1]. Note that the sled goes alongside the rail when the system is in use. Below in figure 5, the width of the entire system can be seen as about 2 feet in this design and configuration [2.1.3].


Figure 5: Top-side view of Assembled system

## 3.3 SYSTEM COMPONENTS

### 3.3.1 Sled


Figure 6: Sled

The sled for my design should have a long but thin base, between 5 and 6 feet in length and below 1.5 feet in width this ensures that the sled will fit in an average American pickup truck [2.2.2]. The dimensions mentioned above should be able to accommodate both a 4-seater sofa and a 5-shelf bookshelf [2.1.2, 2.1.3]. The cylinders will attach to the sled with a bracket (not pictured in figure 6), these cylinders will be free rotating. The brackets will include side braces that will have sections for straps to ensure that the furniture stays on the system. The cylinder must have a large diameter so that with a calculated offset the cylinders will have more than one rolling on steps at a time to go up the stairs smoothly. The last cylinder at the back of the stairs will be designed to have an offset so that when going down the stairs that cylinder will be in contact with the stairs until the system goes down one step. The large diameter and offset of the cylinders allow the system to go up and down a set of stairs repeatedly [2.1.1]. The lifted portion at the front of the sled should not allow for unexpected stopping or hitting of the stairs while going up [2.3.2]. The back of the sled also has an angled support so that furniture cannot slide down the stairs and potentially injure the user and the furniture [2.3.1,2.3.3]. The last component of the sled is the two attachments for the rope that will control the movement of the sled.

### 3.3.2 Joints


Figure 7 : Large Joint

The large joint, pictured above in figure 7, is used to connect the main rail and the rail with the winch on the end of it. These joints would be fitted with notches so that any angle can be set on with the joints. One each end of the joint is square block which are meant to be encased by the rail.

The small joint is very similar to the large joint, this join adheres to the main rail as well as the rail with a pulley on it. Incorporated into the design are holes to insert pins to keep the joint in place when the system is fully assembled.


Figure 8: Small Joint

### 3.3.3 Rails


Figure 9: Stacked Rail Configuration

The rails are designed to hold both the winch and the pulley already fully integrated into the rails. The stacked configuration above, in figure 9, is short enough to fit on top of the sled when it is fully stacked [2.2.2]. In figure 10, the stacked configuration can fit on top of the sled which can make transportation more efficient.


Figure 10: Transportation Configuration

### 3.3.4 Electronics and Block Diagram

This design includes a battery for a power source to be used to power the system, defining this battery as rechargeable allows for the system to be reusable [2.1.4]. Another mentionable component is the sensor in the block diagram below, using the most accurate and precise sensor we can find to ensure that the safety of the system is reliable.


Figure 11 : Component Block Diagram

# 4.0 CONCLUSION

I found that my design was heavily influenced by the patent mentioned above in section 3.1, but the flaws of that design according the system requirements were achieved through my design. There will be calculations needed to ensure that the true design of the system complies with natural forces. Additionally, the stopping mechanism may not be the safest, so that subsystem will need to be looked into further. In my design a mounting system for the rails was overlooked and I think that incorporating right triangles that can slide onto the bottom of the rails might be a great solution.

# 5.0 APPENDIX

No. | Requirement | Verification Description | T | A | O | R
1 | 2.1.1 | Test load and trial | X
2 | 2.1.2 | Measurement/Trial | X
3 | 2.1.3 | Measurement/Trial | X
4 | 2.1.4 | Repeated Trials | X | | X
5 | 2.2.1 | Measurement and Comparison | X | | | X
6 | 2.2.2 | Measurement and Comparison | X | | | X
7 | 2.3.1 | Trial, followed by Analysis and Comparison | X | X | X | X
8 | 2.3.2 | Trial and Observation | X | | X
9 | 2.3.3 | Trial and Observation | X | | X

T – Test and Measurement; A – Analysis and Simulation;
O – Observation and Inspection; R – Reference and Datasheet

(Requirements verification matrix. | download table - researchgate) [2]

# 6.0 REFERENCES

[1] M. B. ME, “Portable Stair Lift System,” PhD Thesis, WORCESTER POLYTECHNIC INSTITUTE, 2021.

[2] “Table 1. Requirements Verification Matrix.,” ResearchGate. Accessed: Sep. 29, 2023. [Online]. Available: https://www.researchgate.net/figure/Requirements-Verification-Matrix_tbl1_269163835

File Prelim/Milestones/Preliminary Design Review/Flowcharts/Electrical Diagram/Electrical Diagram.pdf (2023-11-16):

Motors

Encoder Counters | Motor Drivers
Arduino Due (Motor Control) | Arduino Due (Main board)

Charger

BMS | Battery

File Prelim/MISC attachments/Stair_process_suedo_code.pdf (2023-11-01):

Process for Going up the stairs:

### 1. Set stair parameters and number of stairs 2. Load device 3. Set to rolling mode 4. Roll to bottom of stairs 5. Switch modes to climbing

Robot moves up one step following preset path Preset path for each leg:
i. Round or cornered path from one step to the next

a.

6.

Set robot to rolling mode
a. Roll to the edge of next step

7.

### 8. Repeat process 5-7 until top of stairs are reached

# Suedo Code

Wednesday, November 1, 2023 8:14 AM

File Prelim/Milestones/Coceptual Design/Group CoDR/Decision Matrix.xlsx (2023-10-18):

Criteria | Climbing Ability | Time to climb 1 flight (higher = faster) | Simplicity (higher = simpler) | Part Count (higher = lower #) | Stability | Adaptability | Operator Effort (higher = less effort) | Safety
Weight | 10 | 2 | 5 | 4 | 10 | 6 | 5 | 10 | Score | Best?
Lobed Camshafts | 7 | 3 | 7 | 8 | 8 | 4 | 10 | 7 | 367
6 Legs, 2 2DOF and 4 3DOF | 9 | 8 | 1 | 3 | 10 | 10 | 10 | 10 | 433 | Best!
2 Legs with "Tail" pushing non powered front | 8 | 6 | 6 | 5 | 7 | 8 | 10 | 9 | 400
Centipede On Tracks | 8 | 8 | 4 | 4 | 9 | 7 | 8 | 10 | 404
Powered Treads + Triwheel and Cage + Assisted Lifting | 8 | 8 | 7 | 4 | 9 | 7 | 7 | 10 | 414
Autonomous Robot Legs (2 DOF) | 9 | 8 | 3 | 4 | 8 | 9 | 10 | 10 | 421
Legs Driven By Camshaft | 8 | 4 | 3 | 4 | 9 | 6 | 10 | 10 | 395
Leg Designs |  |  |  |  |  |  |  |  | 0
Natalie/Alex |  | 7 | 6 | 6 | 10 | 9 |  |  | 222
 |  |  |  |  |  |  |  |  | 0
Ian |  | 8 | 5 | 5 | 10 | 10 |  |  | 221
Devin |  | 6 | 7 | 7 | 8 | 8 |  |  | 203

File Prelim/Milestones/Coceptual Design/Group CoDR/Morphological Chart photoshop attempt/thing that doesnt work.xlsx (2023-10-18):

Atlas Team Morphological Chart
Mobility (unpowered)
Mobility (Powered)
Operation
Stability System
Payload System

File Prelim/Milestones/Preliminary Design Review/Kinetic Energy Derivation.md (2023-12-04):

total Kinetic energy:
$$
K = \sum\limits_{i = 1}^{N} K_i
$$

Kinetic Energy of each body:
$$
K_{i} = \frac{1}{2}m_{i}V_{i}^{2}
$$
matrix form:
$$
K_{i}= \frac{1}{2} m_{i} \dot{{^{I}_{I}{\boldsymbol{r}}_{i}}^{\intercal}} \dot{{^{I}_{I}{\boldsymbol{r}}_{i}}}
$$
this scan be expanded and simplified:

$$
K_{i} = \underbrace{\frac{1}{2}m_{i} \dot{{^{I}_{I}{\boldsymbol{r}}_{i}}^{\intercal}} \ \dot{{^{I}_{I}{\boldsymbol{r}}_{i}}} }_{\text{translational}} + \underbrace{\frac{1}{2}\dot{{^{I}_{I}{\boldsymbol{r}}_{i}}^{\intercal}} \dot{{^{I}\boldsymbol{T}}_{\!i}^{\intercal}}{^{i}_{i}\boldsymbol{\Gamma}}}_{Coupling} + \underbrace{\frac{1}{2} trace\left(\dot{{^{I}\boldsymbol{T}}_{\!i}} {^{i}_{i}\boldsymbol{J}}\dot{{^{I}\boldsymbol{T}}_{\!i}^{\intercal}}\right)}_{Rotational}
$$

system mass mtx
$$
H(\boldsymbol{\gamma}) = \frac{\partial}{\partial \ \dot{\boldsymbol{\gamma}}} \left( \frac{\partial K}{\partial \ \dot{\boldsymbol{\gamma}}^{\intercal}} \right)
$$

d = jacobian(jacobian(K, gamma_dot).', gamma)*gamma_dot - jacobian(K, gamma).' ;
$$
\boldsymbol{d}(\boldsymbol{\gamma}, \dot{\boldsymbol{\gamma}}) = \left( \frac{\partial}{\partial \ \boldsymbol{\gamma}}  \left( \frac{\partial \ K}{\partial \ \dot{\boldsymbol{\gamma}}}\right)^{\intercal}\right) \dot{\boldsymbol{\gamma}} \ - \left(\frac{\partial \ K}{\partial \ \boldsymbol{\gamma}}\right)^{\intercal}
$$

potential energy
$$
U_{i} = \begin{bmatrix}0 \\ 0 \\ g\end{bmatrix}^{\intercal} {^{I}_{I}{\boldsymbol{r}}_{i}} m_{i} + {^{I}\boldsymbol{T}}_{\!i} \ {^{i}_{i}\boldsymbol{\Gamma}}
$$

total grav potential
$$
\boldsymbol{U} = \sum\limits_{i = 1}^{N} U_{i}
$$

forces due to grav
G = jacobian(U, gamma).';
$$
\boldsymbol{G} = \frac{\partial \ \boldsymbol{U}}{\partial \ \boldsymbol{\gamma}}
$$

firstly, the ground contact force is calculated in the Inertial frame
```
[diag([0, 0, kP])]*r_IIrP + diag([0, 0, kD])*dot_r_IIrP;
```
$$
{^{I}_{} \boldsymbol{\mathrm{F}}_{P}} = \begin{bmatrix}0 & 0 & 0 \\ 0 & 0 & 0 \\ 0 & 0 & k_{p}\end{bmatrix} {^{I}_{I}{\boldsymbol{r}}_{P}} + \begin{bmatrix}0 & 0 & 0 \\ 0 & 0 & 0 \\ 0 & 0 & k_{D}\end{bmatrix} \dot{{^{I}_{I}{\boldsymbol{r}}_{P}}}
$$

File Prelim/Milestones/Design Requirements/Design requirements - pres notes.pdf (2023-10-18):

requirements:

safety)
no feedback
3) less damage than normal moving:
“less than Average american moving damage” or something like that
maybe just remove #3
reword #3 to be more about personal safety
mention its better for people more, it has to be safer and less strain for the users than
- less health expenses?

Functionality)
repeadatley up and down floor) up OR down
ok

consolidate 6, 7, and 4
“transport 4-seat sofa up and down 1 floor repeatably”

“if we do 6 and 7, we’ve already done 4”??

Interfacing)
be more specific

define #8 by a specific standard

“fits in the back of a moving truck” is too vague, specify the car more or something fit in truck with a couch?

save the width for the specifications

use the IRC code or the equivalent for req #8 about building layouts. possibly remove #8 if it ends up being redundant.

maybe have something about ceiling height?

go through IRC about building layouts.

put “straight stairs” specifically in the problems statement to limit scope from the start. this might be able to replace req#4 since 1 straight stairway would be 1 floor.
“1 flight of stairs” specifically since that would be 1 stairway

SLIDES:
colors: hell yea

design: hell yea

goofy picture is not professional and makes it a joke

show data about injuries and deaths or something like that, a plot or graph or something.

consider talking about wages too, the cost of the system could be less than moving wages + injuriy costs and all that.

match the red Xs to the color scheme, gray, bright blue, something like that.
same blue as the slides with a black outline

align images better.

general feedback)

introductions are supposed to be professional, we need professional photos and business-ey intros like “i’m blah and i’m the lead”, or “i’m blah and I’m doing design work” something like that

don’t forget page numbers.

avoid sunburst/gradient slide backgrounds because visually they’re bad

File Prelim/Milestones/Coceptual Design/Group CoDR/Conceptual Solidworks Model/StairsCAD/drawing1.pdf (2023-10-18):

193.00 7.75 (RD⁴⁾ (RD1); 36.00 ¹⁴⁷.25 (RD²⁾ (12' 7")

SOLIDWORKS Educational Product. For Instructional Use Only.








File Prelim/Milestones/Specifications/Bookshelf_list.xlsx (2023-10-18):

Bookshelf | Weight(lbs) | Width(in) | Depth(in) | Height(in) | Shelves
A-Saratoga | 56.05 | 29.88 | 12.5 | 71.53 | 5
B-Edenbrook | 81 | 31.5 | 12.8 | 72.8 | 5
C-Maple Cross | 76 | 29.56 | 12.81 | 65.21 | 5
D- Cherry | 78.8 | 33 | 11.6 | 59.8 | 5
E - Farini | 86.8 | 33 | 11.6 | 59.8 | 5
F- Rolanstar | 14.03 | 23.62 | 13.78 | 63 | 5
G - Average | 65.44666667 | 30.09333333 | 12.515 | 65.35666667 | 5

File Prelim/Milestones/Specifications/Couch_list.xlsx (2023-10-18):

Couch | Weight(lbs) | Width(in) | Depth(in) | Height(in) | Seats
A-Leisland | 120 | 88.58 | 33.07 | 27.5 | 3
B-Van Acc | 100 | 89 | 36 | 35 | 3
C-Ashley | 238 | 88 | 36 | 40 | 3
D-Mcombo | 250 | 92 | 36 | 41 | 3
E-Williams Space | 330 | 91 | 34.3 | 35 | 4
F-Amazon | 136.24 | 88.98 | 42.13 | 31.5 | 4
G-Zafly | 185.36 | 116.5 | 31.9 | 33.5 | 4
H-Jennifer Taylor | 110 | 88 | 37 | 32.5 | 3
I-Average | 183.7 | 92.7575 | 35.8 | 34.5 | 3.375

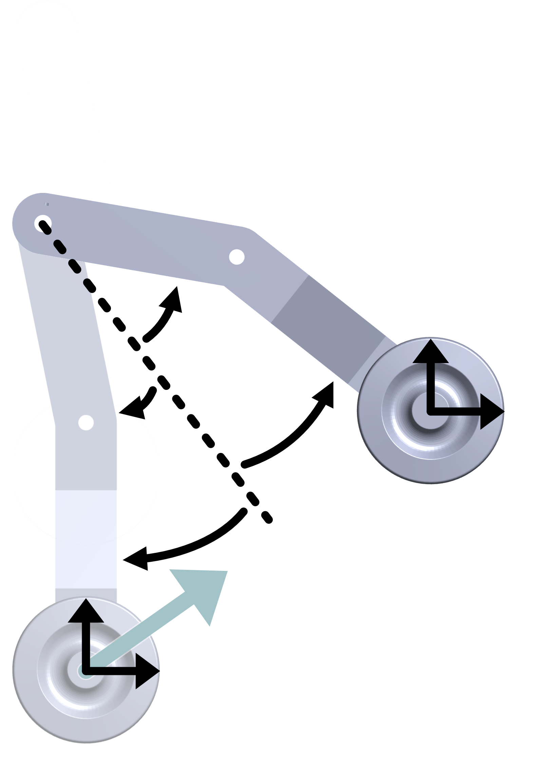
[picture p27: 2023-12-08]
Prelim/Milestones/Preliminary Design Review/Presentation/Attachments/slide 2B.png

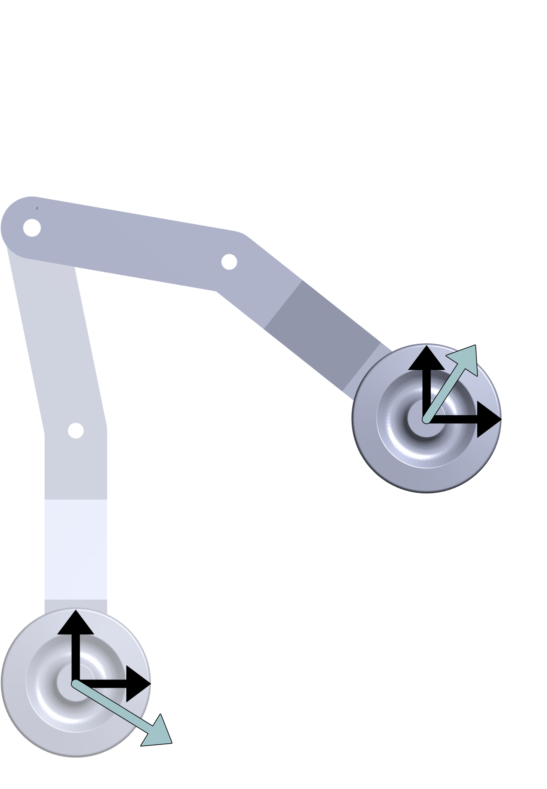
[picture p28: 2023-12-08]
Prelim/Milestones/Preliminary Design Review/Presentation/Attachments/slide 3.png

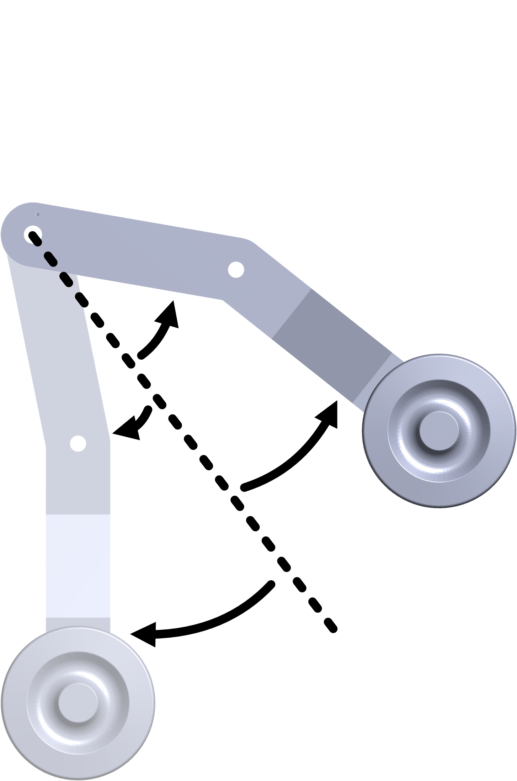
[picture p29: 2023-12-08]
Prelim/Milestones/Preliminary Design Review/Presentation/Attachments/IK_2.png

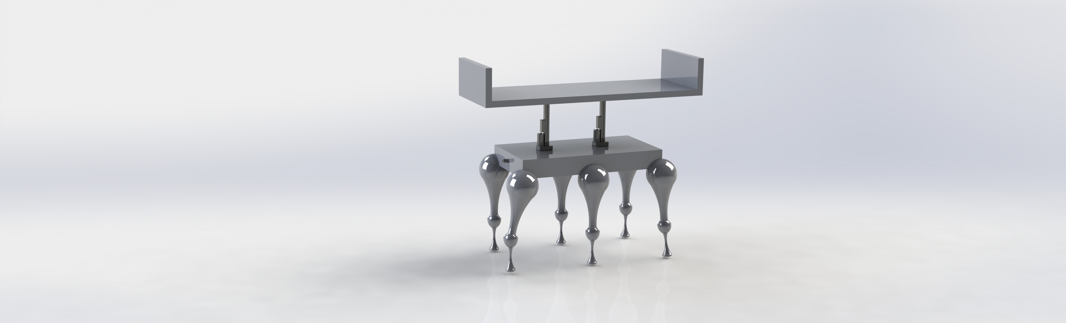
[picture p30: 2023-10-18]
Prelim/Milestones/Coceptual Design/Indiv CoDR/Ian CoDR/Ian_RobotLegDesign/systemRender.JPG

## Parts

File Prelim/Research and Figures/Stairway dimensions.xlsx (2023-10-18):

 |  |  | landing width same as stairs?
Name of stairs | Height of total stairs | Tread depth (including Nosing depth protrusion) | yes/no | Bottoms Landing depth | Upper Landing Depth( including bottom Nosing depth) | 2nd flight upper landing depth if applicable | Step height (riser height) (including nosing vertical protrusion) | Head room | Nosing Height | Nosing depth protrusion | Nosing Vertical Protrusion | stairway width | width between handrails | handrail number: 0, 1, 2
Stem inside back stairs | 69 | 11.75 | yes | 71 | 68.5 | n/a | 7.25 | 121 | 1.75 | 5/8th in | negligible | 58in | 55in | 2
stem outside back staris | 75.5 | 11.25 | yes | inf | large enough | n/a | 5.75 | inf | 0 | 0 | 0 | 96.5 | 90 | 2
Stem inside front stairs | 130 | 11.9375 | yes | 88.5 | 48.5 | 72 | 7 | inf | 0 | 1 | 0 | 72 | 66 | 2
Stem outside front stairs to AC1

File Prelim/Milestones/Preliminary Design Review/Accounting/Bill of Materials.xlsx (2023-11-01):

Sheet: Request 1 8-18 867.40
COE Purchase Request Form |  |  |  |  |  |  | Fill in below if you are maintaining a budget:
 | Requestor Name: |  |  | If you have any questions or suggestions about this form, please email Ginger ASAP at macgowav@erau.edu |  |  |  |  |  | Funds Allocated: | $1000.00
 | Requestor Email: |  |  |  |  |  |  |  |  | Previous Expenses: | $0.00
 | Requestor Phone: |  |  |  |  |  |  |  |  | Today's Expenses: | $867.40
 | Request Date: |  |  |  |  |  |  |  |  | Cumulative Expenses: | $867.40
 |  |  |  |  |  |  |  |  |  | Remaining Balance: | $132.60
 | Please be sure you have received and forwarded approval from Environmental Health and Safety (EHS) for hazardous materials to Ginger at macgowav@erau.edu or insert a copy in this spreadsheet.
Actual Order Date | Vendor Name | Part Number and/ or Description | Link | Price Each | QTY | Extended Price | Shipping | Tax | Other | Item Total | Vendor and Request Totals
 |  |  |  | $0.00 |  | $0.00 | $0.00 | $0.00 | $0.00 | $0.00
 |  |  |  | $0.00 |  | $0.00 | $0.00 | $0.00 | $0.00 | $0.00
 |  |  |  | $0.00 |  | $0.00 | $0.00 | $0.00 | $0.00 | $0.00
 |  |  |  | $0.00 |  | $0.00 | $0.00 | $0.00 | $0.00 | $0.00
 |  |  |  | $0.00 |  | $0.00 | $0.00 | $0.00 | $0.00 | $0.00
 |  |  |  | $0.00 |  | $0.00 | $0.00 | $0.00 | $0.00 | $0.00
 |  |  |  | $0.00 |  | $0.00 | $0.00 | $0.00 | $0.00 | $0.00
 |  |  |  |  |  |  | HAZMAT /Fees: | $0.00 | $0.00 | $0.00
 |  |  |  |  |  |  |  |  |  | Vendor Total: | $0.00
EXAMPLE | www.featherweightaltimeters.com | SKU: GPS_3-way: Featherweight GPS Tracker (upd), 3-unit system (GS + 2 trackers + 2 batteries) | https://www.featherweightaltimeters.com/store/p22/Featherweight_GPS_Tracker_%28upd%29.html | $120.00 | 1 | $120.00 | $0.00 | $0.00 | $0.00 | $120.00
8/18/2022 Ginger will fill dates in |  | SKU: GPS_3-way: Extra batteries) | https://www.featherweightaltimeters.com/store/p22/Featherweight_GPS_Tracker_%28upd%29.html | $300.00 | 2 | $600.00 | $0.00 | $0.00 | $0.00 | $600.00
 |  |  | PLEASE NOTE SALE Price with code SU2022 ** Save $24** |  |  | $0.00 | $0.00 | $0.00 | -$24.00 | -$24.00
 |  |  |  |  |  | $0.00 | $0.00 | $0.00 | $0.00 | $0.00
 |  |  |  |  |  | $0.00 | $0.00 | $0.00 | $0.00 | $0.00
 |  |  |  |  |  | $0.00 | $0.00 | $0.00 | $0.00 | $0.00
 |  |  |  |  |  | $0.00 | $10.00 | $0.00 | $0.00 | $10.00
 |  |  |  |  |  |  |  | $11.40 | $0.00 | $11.40
 |  |  |  |  |  |  | HAZMAT /Fees: | $25.00 | $125.00 | $150.00
 |  |  |  |  |  |  |  |  |  | Vendor Total: | $867.40
 |  |  |  | $0.00 | 0 | $0.00 | $0.00 | $0.00 | $0.00 | $0.00
 |  |  |  | $0.00 | 0 | $0.00 | $0.00 | $0.00 | $0.00 | $0.00
 |  |  |  | $0.00 | 0 | $0.00 | $0.00 | $0.00 | $0.00 | $0.00
 |  |  |  | $0.00 | 0 | $0.00 | $0.00 | $0.00 | $0.00 | $0.00
 |  |  |  | $0.00 | 0 | $0.00 | $0.00 | $0.00 | $0.00 | $0.00
 |  |  |  | $0.00 | 0 | $0.00 | $0.00 | $0.00 | $0.00 | $0.00
 |  |  |  | $0.00 | 0 | $0.00 | $0.00 | $0.00 | $0.00 | $0.00
 |  |  |  |  |  |  | HAZMAT /Fees: | $0.00 | $0.00 | $0.00
 |  |  |  |  |  |  |  |  |  | Vendor Total: | $0.00
 |  |  |  | $0.00 | 0 | $0.00 | $0.00 | $0.00 | $0.00 | $0.00
 |  |  |  | $0.00 | 0 | $0.00 | $0.00 | $0.00 | $0.00 | $0.00
 |  |  |  | $0.00 | 0 | $0.00 | $0.00 | $0.00 | $0.00 | $0.00
 |  |  |  | $0.00 | 0 | $0.00 | $0.00 | $0.00 | $0.00 | $0.00
 |  |  |  | $0.00 | 0 | $0.00 | $0.00 | $0.00 | $0.00 | $0.00
 |  |  |  | $0.00 | 0 | $0.00 | $0.00 | $0.00 | $0.00 | $0.00
 |  |  |  | $0.00 | 0 | $0.00 | $0.00 | $0.00 | $0.00 | $0.00
 |  |  |  |  |  |  | HAZMAT /Fees: | $0.00 | $0.00 | $0.00
 |  |  |  |  |  |  |  |  |  | Vendor Total: | $0.00
 |  |  |  | $0.00 | 0 | $0.00 | $0.00 | $0.00 | $0.00 | $0.00
 |  |  |  | $0.00 | 0 | $0.00 | $0.00 | $0.00 | $0.00 | $0.00
 |  |  |  | $0.00 | 0 | $0.00 | $0.00 | $0.00 | $0.00 | $0.00
 |  |  |  | $0.00 | 0 | $0.00 | $0.00 | $0.00 | $0.00 | $0.00
 |  |  |  | $0.00 | 0 | $0.00 | $0.00 | $0.00 | $0.00 | $0.00
 |  |  |  | $0.00 | 0 | $0.00 | $0.00 | $0.00 | $0.00 | $0.00
 |  |  |  | $0.00 | 0 | $0.00 | $0.00 | $0.00 | $0.00 | $0.00
 |  |  |  |  |  |  | HAZMAT /Fees: | $0.00 | $0.00 | $0.00
 |  |  |  |  |  |  |  |  |  | Vendor Total: | $0.00
 |  |  |  | $0.00 | 0 | $0.00 | $0.00 | $0.00 | $0.00 | $0.00
 |  |  |  | $0.00 | 0 | $0.00 | $0.00 | $0.00 | $0.00 | $0.00
 |  |  |  | $0.00 | 0 | $0.00 | $0.00 | $0.00 | $0.00 | $0.00
 |  |  |  | $0.00 | 0 | $0.00 | $0.00 | $0.00 | $0.00 | $0.00
 |  |  |  | $0.00 | 0 | $0.00 | $0.00 | $0.00 | $0.00 | $0.00
 |  |  |  | $0.00 | 0 | $0.00 | $0.00 | $0.00 | $0.00 | $0.00
 |  |  |  | $0.00 | 0 | $0.00 | $0.00 | $0.00 | $0.00 | $0.00
 |  |  |  |  |  |  | HAZMAT /Fees: | $0.00 | $0.00 | $0.00
 |  |  |  |  |  |  |  |  |  | Vendor Total: | $0.00
 |  |  |  |  |  |  |  |  |  | Purchase Request Total: | $867.40

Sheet: Request 8-25 100.00
COE Purchase Request Form |  |  |  |  |  |  | Fill in below if you are maintaining a budget:
 | Requestor Name: |  |  | If you have any questions or suggestions about this form, please email Ginger ASAP at macgowav@erau.edu |  |  |  |  |  | Funds Allocated: | $1000.00
 | Requestor Email: |  |  |  |  |  |  |  |  | Previous Expenses: | $867.40
 | Requestor Phone: |  |  |  |  |  |  |  |  | Today's Expenses: | $100.00
 | Request Date: |  |  |  |  |  |  |  |  | Cumulative Expenses: | $967.40
 |  |  |  |  |  |  |  |  |  | Remaining Balance: | $32.60 | COE Request APPROVER SECTION, Approvers Please fill in below, if data applies to all items only fill top line
 | Please be sure you have received and forwarded approval from Environmental Health and Safety (EHS) for hazardous materials to Ginger at macgowav@erau.edu or insert a copy in this spreadsheet. |  |  |  |  |  |  |  |  |  |  |  |  | COE Request APPROVER Name and email:
Actual Order Date | Vendor Name | Part Number and/ or Description | Link | Price Each | QTY | Extended Price | Shipping | Tax | Other | Item Total | Vendor and Request Totals | Cost Center | Spend Category | Classe(s) to be Used For | Lab(s) to be Used In | Projects to be Used For | Bldg & Room # Used In | Delivery Location
 |  |  |  | $0.00 |  | $0.00 | $0.00 | $0.00 | $0.00 | $0.00
 |  |  |  | $0.00 |  | $0.00 | $0.00 | $0.00 | $0.00 | $0.00
 |  |  |  | $0.00 |  | $0.00 | $0.00 | $0.00 | $0.00 | $0.00
 |  |  |  | $0.00 |  | $0.00 | $0.00 | $0.00 | $0.00 | $0.00
 |  |  |  | $0.00 |  | $0.00 | $0.00 | $0.00 | $0.00 | $0.00
 |  |  |  | $0.00 |  | $0.00 | $0.00 | $0.00 | $0.00 | $0.00
 |  |  |  | $0.00 |  | $0.00 | $0.00 | $0.00 | $0.00 | $0.00
 |  |  |  |  |  |  | HAZMAT /Fees: | $0.00 | $0.00 | $0.00
 |  |  |  |  |  |  |  |  |  | Vendor Total: | $0.00
EXAMPLE | www.featherweightaltimeters.com | SKU: GPS_3-way: Featherweight GPS Tracker (upd), 3-unit system (GS + 2 trackers + 2 batteries) | https://www.featherweightaltimeters.com/store/p22/Featherweight_GPS_Tracker_%28upd%29.html | $50.00 | 1 | $50.00 | $0.00 | $0.00 | $0.00 | $50.00 |  | 42714 | Instructional Supplies | ME312, 313, 314 | Materials and LMS Labs | Prescott Eagle Works | Bldg 75 AXFAB Rm's 115, 125, 135 | Bldg 75 AXFAB Rm 115
2022-08-25 |  | SKU: GPS_3-way: Extra batteries) | https://www.featherweightaltimeters.com/store/p22/Featherweight_GPS_Tracker_%28upd%29.html | $25.00 | 2 | $50.00 | $0.00 | $0.00 | $0.00 | $50.00 |  | 42714 | Instructional Supplies | ME312, 313, 314 | Materials and LMS Labs | Prescott Eagle Works | Bldg 72 STEM Rm 115 | Bldg 75 AXFAB Rm 115
 |  |  |  |  |  | $0.00 | $0.00 | $0.00 | $0.00 | $0.00
 |  |  |  |  |  | $0.00 | $0.00 | $0.00 | $0.00 | $0.00
 |  |  |  |  |  | $0.00 | $0.00 | $0.00 | $0.00 | $0.00
 |  |  |  |  |  | $0.00 | $0.00 | $0.00 | $0.00 | $0.00
 |  |  |  |  |  | $0.00 | $0.00 | $0.00 | $0.00 | $0.00
 |  |  |  |  |  |  |  | $0.00 | $0.00 | $0.00
 |  |  |  |  |  |  | HAZMAT /Fees: | $0.00 | $0.00 | $0.00
 |  |  |  |  |  |  |  |  |  | Vendor Total: | $100.00
 |  |  |  | $0.00 | 0 | $0.00 | $0.00 | $0.00 | $0.00 | $0.00
 |  |  |  | $0.00 | 0 | $0.00 | $0.00 | $0.00 | $0.00 | $0.00
 |  |  |  | $0.00 | 0 | $0.00 | $0.00 | $0.00 | $0.00 | $0.00
 |  |  |  | $0.00 | 0 | $0.00 | $0.00 | $0.00 | $0.00 | $0.00
 |  |  |  | $0.00 | 0 | $0.00 | $0.00 | $0.00 | $0.00 | $0.00
 |  |  |  | $0.00 | 0 | $0.00 | $0.00 | $0.00 | $0.00 | $0.00
 |  |  |  | $0.00 | 0 | $0.00 | $0.00 | $0.00 | $0.00 | $0.00
 |  |  |  |  |  |  | HAZMAT /Fees: | $0.00 | $0.00 | $0.00
 |  |  |  |  |  |  |  |  |  | Vendor Total: | $0.00
 |  |  |  | $0.00 | 0 | $0.00 | $0.00 | $0.00 | $0.00 | $0.00
 |  |  |  | $0.00 | 0 | $0.00 | $0.00 | $0.00 | $0.00 | $0.00
 |  |  |  | $0.00 | 0 | $0.00 | $0.00 | $0.00 | $0.00 | $0.00
 |  |  |  | $0.00 | 0 | $0.00 | $0.00 | $0.00 | $0.00 | $0.00
 |  |  |  | $0.00 | 0 | $0.00 | $0.00 | $0.00 | $0.00 | $0.00
 |  |  |  | $0.00 | 0 | $0.00 | $0.00 | $0.00 | $0.00 | $0.00
 |  |  |  | $0.00 | 0 | $0.00 | $0.00 | $0.00 | $0.00 | $0.00
 |  |  |  |  |  |  | HAZMAT /Fees: | $0.00 | $0.00 | $0.00
 |  |  |  |  |  |  |  |  |  | Vendor Total: | $0.00
 |  |  |  | $0.00 | 0 | $0.00 | $0.00 | $0.00 | $0.00 | $0.00
 |  |  |  | $0.00 | 0 | $0.00 | $0.00 | $0.00 | $0.00 | $0.00
 |  |  |  | $0.00 | 0 | $0.00 | $0.00 | $0.00 | $0.00 | $0.00
 |  |  |  | $0.00 | 0 | $0.00 | $0.00 | $0.00 | $0.00 | $0.00
 |  |  |  | $0.00 | 0 | $0.00 | $0.00 | $0.00 | $0.00 | $0.00
 |  |  |  | $0.00 | 0 | $0.00 | $0.00 | $0.00 | $0.00 | $0.00
 |  |  |  | $0.00 | 0 | $0.00 | $0.00 | $0.00 | $0.00 | $0.00
 |  |  |  |  |  |  | HAZMAT /Fees: | $0.00 | $0.00 | $0.00
 |  |  |  |  |  |  |  |  |  | Vendor Total: | $0.00
 |  |  |  | $0.00 | 0 | $0.00 | $0.00 | $0.00 | $0.00 | $0.00
 |  |  |  | $0.00 | 0 | $0.00 | $0.00 | $0.00 | $0.00 | $0.00
 |  |  |  | $0.00 | 0 | $0.00 | $0.00 | $0.00 | $0.00 | $0.00
 |  |  |  | $0.00 | 0 | $0.00 | $0.00 | $0.00 | $0.00 | $0.00
 |  |  |  | $0.00 | 0 | $0.00 | $0.00 | $0.00 | $0.00 | $0.00
 |  |  |  | $0.00 | 0 | $0.00 | $0.00 | $0.00 | $0.00 | $0.00
 |  |  |  | $0.00 | 0 | $0.00 | $0.00 | $0.00 | $0.00 | $0.00
 |  |  |  |  |  |  | HAZMAT /Fees: | $0.00 | $0.00 | $0.00
 |  |  |  |  |  |  |  |  |  | Vendor Total: | $0.00
 |  |  |  |  |  |  |  |  |  | Purchase Request Total: | $100.00

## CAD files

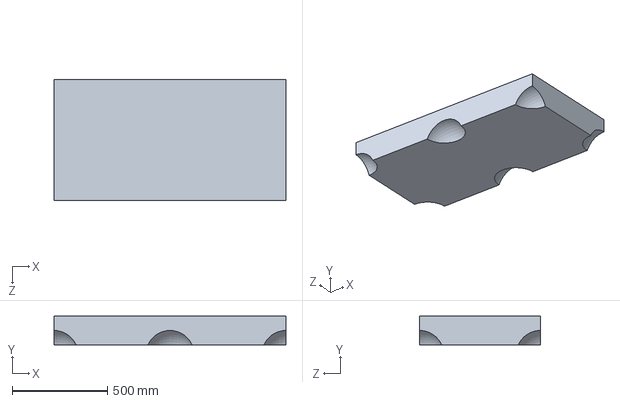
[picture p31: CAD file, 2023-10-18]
Prelim/Milestones/Coceptual Design/Indiv CoDR/Ian CoDR/Ian_RobotLegDesign/mainBody.SLDPRT
1219.2 x 152.4 x 635.0 mm

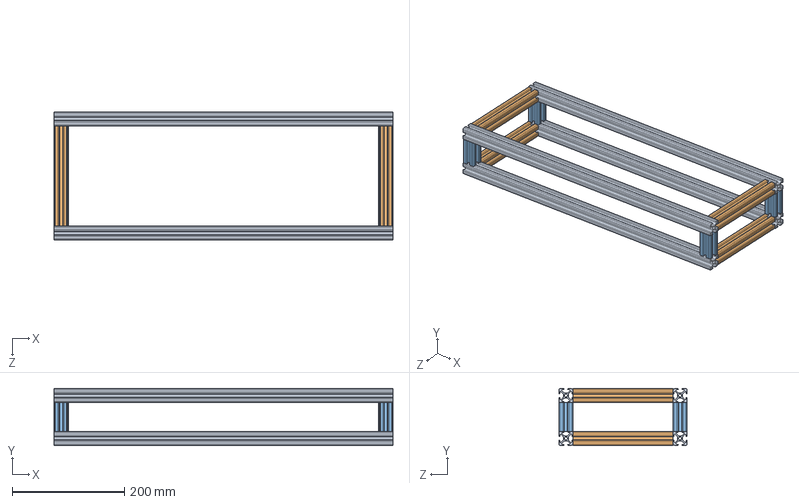
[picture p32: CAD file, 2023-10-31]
Prelim/CAD Model Oct 30/ATLAS_full_Skeleton.SLDASM
603.2 x 101.6 x 228.6 mm
47065T209_T-Slotted-23.75 x 4
47065T411_T-Slotted_9in x 4
47065T553_T-Slotted_2in x 4

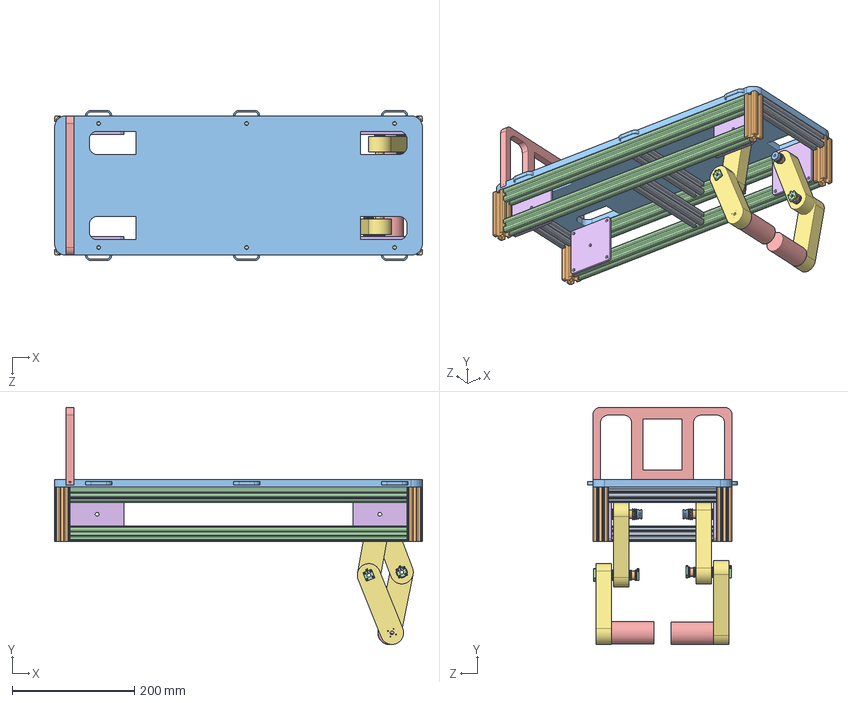
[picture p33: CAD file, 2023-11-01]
Prelim/Milestones/Preliminary Design Review/CAD/CAD Parts Oct 31/Full Assembly 2.SLDASM
603.2 x 389.0 x 246.4 mm
7 In Bar x 4
5 In Bar x 4
21 In Bar x 4
Backing
Mounting Plate x 4
Leg Segment x 4
5909K23_Needle-Roller Thrust Bearing x 8
5909K231_0.032 Thick Washer for 1-4 Shaft Diameter Needle-Roller Thrust Bearing x 16
SDP_sdpsi_a_6p_9-0801508.stp x 4
guide pulley x 2
Square Clamp x 4
Lowresmotor x 2

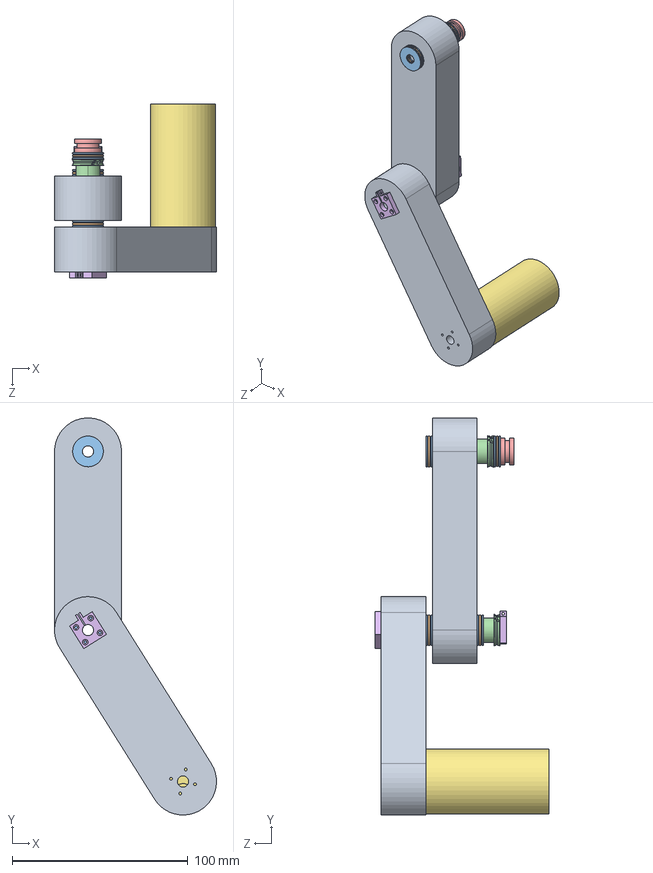
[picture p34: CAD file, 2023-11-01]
Prelim/Milestones/Preliminary Design Review/CAD/CAD Parts Oct 31/Leg Assembly 2.SLDASM
92.1 x 225.7 x 99.0 mm
Leg Segment x 2
5909K23_Needle-Roller Thrust Bearing x 4
5909K231_0.032 Thick Washer for 1-4 Shaft Diameter Needle-Roller Thrust Bearing x 8
SDP_sdpsi_a_6p_9-0801508.stp x 2
guide pulley
Square Clamp x 2
Lowresmotor

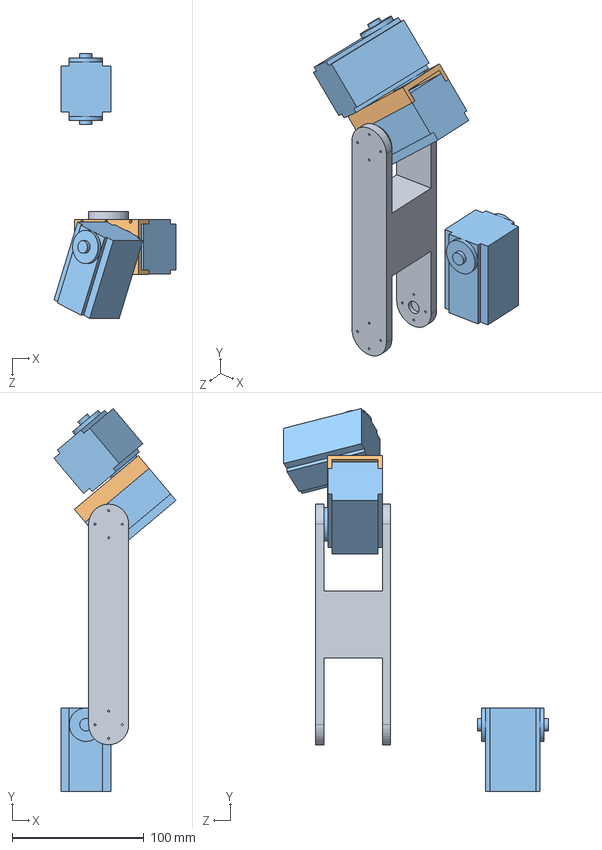
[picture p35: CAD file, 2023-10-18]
Prelim/Milestones/Coceptual Design/Group CoDR/Conceptual Solidworks Model/Leg Assembly.SLDASM
92.7 x 291.1 x 201.1 mm
Leg Bracket
Shoulder
Rough Servo x 3

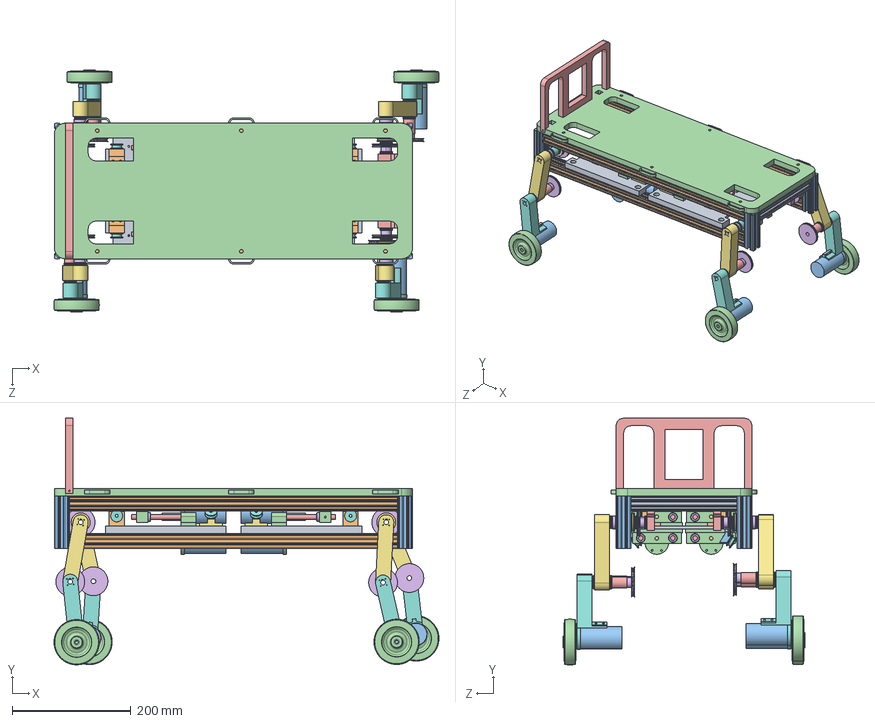
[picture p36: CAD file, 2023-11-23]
Prelim/Milestones/Preliminary Design Review/CAD/MATLAB CAD Files/Full Assembly 3.SLDASM
648.0 x 415.2 x 407.5 mm
7 In Bar x 3
21 In Bar x 4
5 In Bar x 4
Backing
Skateboard Bearing x 18
Leg Segment x 4
Leg Segment Bottom x 4
5909K3_Needle-Roller Thrust Bearing x 26
5909K295_1 mm Thick Washer for 8 mm Shaft Diameter Needle-Roller Thrust Bearing x 52
Lowresmotor x 12
2337T41_Rubber Wheel x 4
Spacer x 4
SDP_sdpsi_a_6p_9m1003008.stp x 8
Idle Pulley x 4
Spacer 3 Quart x 4
Interior Motor Bracket x 2
Lowres Motor Screw x 8
Motor Screw Adapter x 8
Motor Bracket x 8
Guide Shaft x 16
Linear Bearing x 16
Small Bearing Bracket x 8
Motor Pulley x 14
Small Bearing x 14
Pulley Stand 2 x 4
Small Bearing Bracket (Lower) x 2
Central Screw x 8
Pulley Support Bracket x 2

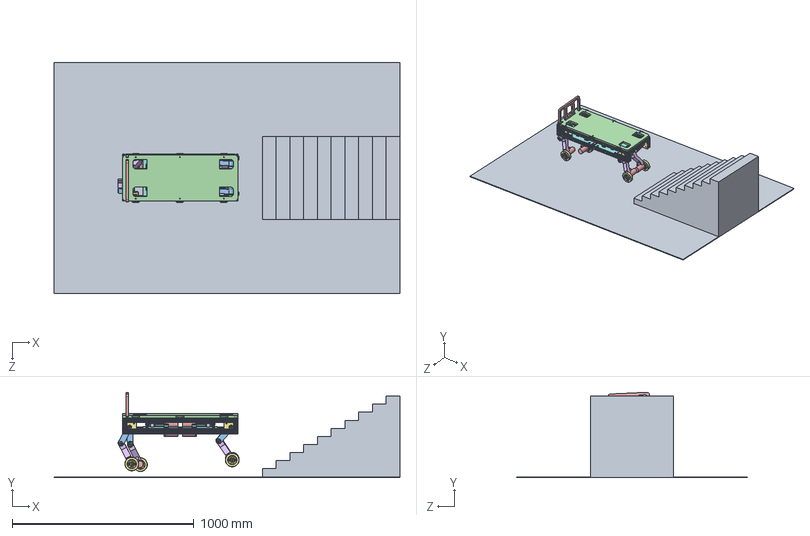
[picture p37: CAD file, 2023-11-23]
Prelim/Milestones/Preliminary Design Review/CAD/MATLAB CAD Files/Stair Climbing Assembly.SLDASM
1905.0 x 470.5 x 1270.0 mm
Stairs Model
21 In Bar x 4
5 In Bar x 4
Backing
47065T801_T-Slotted Framing x 3
Mounting Plate x 4
Skateboard Bearing x 36
5909K3_Needle-Roller Thrust Bearing x 16
5909K295_1 mm Thick Washer for 8 mm Shaft Diameter Needle-Roller Thrust Bearing x 32
Leg Segment Top (Spring) x 4
Idle Pulley x 8
Lowresmotor x 12
Leg Bottom Segment (Spring) x 4
2337T41_Rubber Wheel x 4
Interior Motor Bracket x 2
Lowres Motor Screw x 8
Motor Screw Adapter x 8
Motor Bracket x 8
Guide Shaft x 16
Linear Bearing x 16
Central Screw x 8
Small Bearing Stand NOV 15 x 4
Small Pulley x 16
Small Bearing x 16
Small Bottom Bearing Stand NOV 15 - Copy x 4

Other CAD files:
Prelim/CAD Model Oct 30/Guide Pulley.SLDPRT
Prelim/CAD Model Oct 30/Leg Pulley.SLDPRT
Prelim/CAD Model Oct 30/Leg Segment (FINAL).SLDPRT
Prelim/CAD Model Oct 30/Leg Segment Bottom (FINAL).SLDPRT
Prelim/Milestones/Coceptual Design/Group CoDR/Conceptual Solidworks Model/Foot Bracket.SLDPRT
Prelim/Milestones/Coceptual Design/Group CoDR/Conceptual Solidworks Model/Foot.SLDPRT
Prelim/Milestones/Coceptual Design/Group CoDR/Conceptual Solidworks Model/Leg Bracket.SLDPRT
Prelim/Milestones/Coceptual Design/Group CoDR/Conceptual Solidworks Model/MX-64AT.stl
Prelim/Milestones/Coceptual Design/Group CoDR/Conceptual Solidworks Model/Platform.SLDPRT
Prelim/Milestones/Coceptual Design/Group CoDR/Conceptual Solidworks Model/Rough Servo.SLDPRT
Prelim/Milestones/Coceptual Design/Group CoDR/Conceptual Solidworks Model/Shoulder.SLDPRT
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

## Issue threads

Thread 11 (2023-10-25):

PCB Layout

Natgonz613, 2023-10-25:

Natgonz613, 2023-11-17:
Put all encoder chips on PCB

Ian-q, 2023-11-17:
https://www.digikey.com/en/products/filter/counters-dividers/731?s=N4IgTCBcDaII4FcCGATATkgLgtBTEAugL5A

Ian-q, 2023-11-17:
need a voltage regulator prob

Closed 2023-12-13.

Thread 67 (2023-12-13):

PCB Design for Encoder Counter chips - SEE README

Ian-q, 2023-12-13:
# Requirements:
- [ ] Single board
- [ ] holds all 12 encoder counters
- [ ] has over current protection built in
- [ ] is fully interfacing safe, meaning reverse voltage safe, over current safe, fully idiot proof.
- [ ] should have _vias_ or scrapable traces all over the place, so that if something needs to be re-wired it can be without making a whole new board.

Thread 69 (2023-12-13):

Decide PWM frequency for motors

Ian-q, 2023-12-13:

Ian-q, 2023-12-13:
https://electronics.stackexchange.com/questions/242293/is-there-an-ideal-pwm-frequency-for-dc-brush-motors

Ian-q, 2023-12-22:
For now we'll use 20KHz as the motor PWM frequency.

Ian-q, 2023-12-26:
in default Arduino you can't adjust the PWM frequency itself, so its just the default of 1KHz for now

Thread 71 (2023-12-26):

Duty Cycle PWM Code

Ian-q, 2023-12-26:

Ian-q, 2023-12-26:
Can only use 1KHz signal for now, but I understand the Arduino stuff now so its good for now

Closed 2023-12-26.

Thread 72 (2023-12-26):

Figure out how to use the motor driver

Ian-q, 2023-12-26:

Ian-q, 2023-12-26:
We need to use single channel mode to avoid over-current issues

Ian-q, 2024-01-03:
I need to solder it because the pins are hard to connect, but all we need to do is use a little pin jumper to put it in single channel mode, and then give the proper inputs/outputs.

Closed 2024-01-03.

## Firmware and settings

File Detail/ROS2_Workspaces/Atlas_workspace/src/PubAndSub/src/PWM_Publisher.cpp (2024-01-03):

#include <chrono>
#include <iostream>
#include <memory>
#include "rclcpp/rclcpp.hpp"
#include "std_msgs/msg/int32.hpp"

class PWMPublisher : public rclcpp::Node {
public:
    PWMPublisher() : Node("pwm_publisher") {
        publisher_ = this->create_publisher<std_msgs::msg::Int32>("pwm_topic", 10);
        timer_ = this->create_wall_timer(std::chrono::milliseconds(1000),
                                                                         std::bind(&PWMPublisher::publishPWM, this));
    }

private:
    void publishPWM() {
        auto message = std::make_unique<std_msgs::msg::Int32>();
        message->data = rand() % 101; // Generate a random number from 0 to 100
        publisher_->publish(std::move(message));
    }

    rclcpp::Publisher<std_msgs::msg::Int32>::SharedPtr publisher_;
    rclcpp::TimerBase::SharedPtr timer_;
};

int main(int argc, char **argv) {
    rclcpp::init(argc, argv);
    auto node = std::make_shared<PWMPublisher>();
    rclcpp::spin(node);
    rclcpp::shutdown();
    return 0;
}

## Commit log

2023-10-18 added all existing files
    [2DOF Leg.SLDASM, 6530K118_High-Force Electric Actuator.SLDPRT, Assebly 2.SLDASM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]
2023-10-27 added sample function header for Matlab functions
2023-10-31 cad folder
2023-10-31 fixed aluminum extrusions not working in assembly
    [Frame.SLDASM, Full Assembly.SLDASM]
2023-10-31 added Syncromesh parts
    [SDP_sdpsi_a_6p_9-1201512.SLDPRT, SDP_sdpsi_a_6p_9-1201512.x_t]
2023-11-01 syncromesh files
    [SDP_sdpsi_a_6p_9-0801508.stp, SDP_sdpsi_a_6p_9-1201512.SLDPRT, SDP_sdpsi_a_6p_9-1201512.x_t]
2023-11-02 Uploading November 1st Pseudo Final CAD Files
    Consult the to-do list file for incomplete/optional features to implement
    [1556A63_Zinc-Plated Steel Corner Bracket.SLDPRT, 21 In Bar.SLDPRT, 2337T41_Rubber Wheel.SLDPRT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]
2023-11-03 update dynamics function and update CAD to have local coordinate frames
    [2337T41_Rubber Wheel.SLDPRT, 2337T41_Rubber Wheel.STL, Leg Segment Bottom.SLDPRT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]
2023-11-04 misc
    removed autosave files, exported atlas files for use in matlab, updated matlab simulation code
    [2337T41_Rubber Wheel.SLDPRT, Atlas_Frame.STL, Atlas_Leg_1.STL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]
2023-11-04 remove matlab simulation
    [2337T41_Rubber Wheel.STL, Atlas_Frame.STL, Atlas_Leg_1.STL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]
2023-11-06 misc small updates
    [2337T41_Rubber Wheel.SLDPRT, Leg Segment Bottom.SLDPRT, Leg Segment.SLDPRT]
2023-11-06 Update Leg Segment Bottom.SLDPRT
    [Leg Segment Bottom.SLDPRT]
2023-11-06 Update Full Assembly.SLDASM
2023-11-07 update cad
    [Leg Segment.SLDPRT]
2023-11-15 Create Flowcharts
2023-11-16 Electrical Schematic Rev 1
2023-11-23 cad update
    [1556A63_Zinc-Plated Steel Corner Bracket.SLDPRT, 21 In Bar.SLDPRT, 2337T41_Rubber Wheel.SLDPRT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]
2023-11-23 zip old CAD
    [1556A63_Zinc-Plated Steel Corner Bracket.SLDPRT, 21 In Bar.SLDPRT, 2337T41_Rubber Wheel.SLDPRT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]
2023-11-23 fix CAD organization
    [21 In Bar.SLDPRT, 2337T41_Rubber Wheel.SLDPRT, 47065T801_T-Slotted Framing.SLDPRT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]
2023-12-20 Update Arduino include paths
2023-12-26 create basic ros project directory and start arduino code
2023-12-26 organize datasheets start work on motor driver
2024-01-01 Update include statements in PWM_Publisher.cpp and add dependencies in package.xml
2024-01-16 Create CAD Models
